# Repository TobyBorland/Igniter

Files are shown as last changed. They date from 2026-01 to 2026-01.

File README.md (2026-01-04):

# Igniter
Analogue igniter circuit for transistorised ignition with mechanical advance

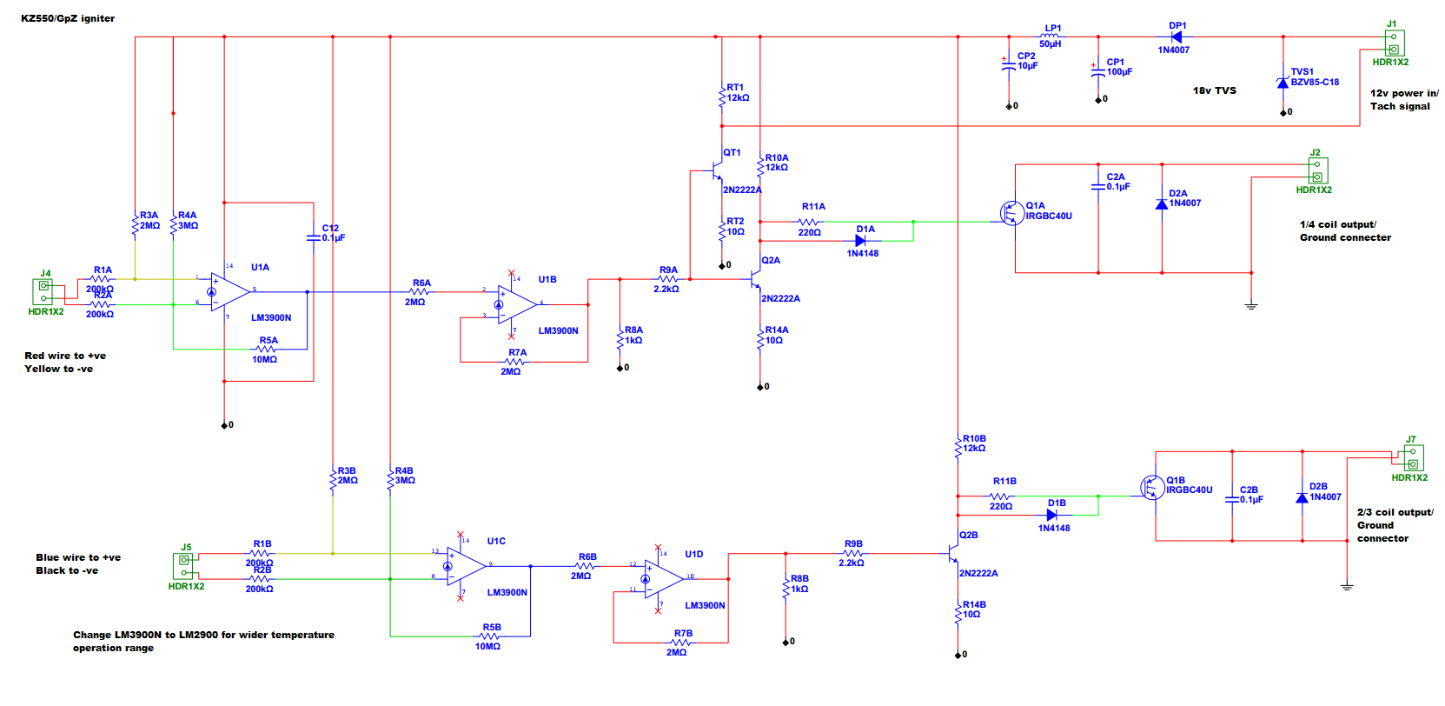
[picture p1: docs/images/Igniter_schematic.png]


### Kettering ignition
This project replaces the igniter used in earlier transistorised Kettering vehicle ignition. 
Old **points** ignition systems use a form of transformer (commonly referred to as an ignition coil) to create a spark for a petrol engine. 
During operation, the low-tension (LT) coil in this transformer is energised with 12 volts, creating a magnetic field. 
When the spark is required, the power is cut to the low-voltage coil, and the magnetic field in the coil transformer collapses, sending energy through the coupled high-tension coil. 
The high-tension coil output has lower resistance to current flow than the low-tension coil as it has more windings and generates higher voltage at lower amps, allowing the circuit to flow through a sparkplug air gap rather than the low-tension coil circuit. This Kettering system is simple and the current through the LT coil can be switched with a mechanical switch, "points" following a cam driven by the engine. A capacitor (**condensor**) is added to the 12v side of the circuit to give the points sufficient time to create a large air gap and force energy discharge through the HT side of the coil transformer. 
The timing of this spark ignition changes relative to the rotational speed of the engine; ignition occurs just after the piston starts a downward cycle in order to reduce mechanical shock. The optimal time to ignite the fuel mixture after the pistons change in direction varies with engine speed, Kettering mechanical systems use a simple mechanical spark advance mechanism which alters the switching points position relative to the cam operating the switch. The cam profile is designed to provide current to the coil for enough time to create a magnetic field powerful enough for an adequate spark. This field generation time is known as **dwell**.
However, switching several amps of current through mechanical contacts at several thousand cycles per minute causes wear and spark erosion. These switch point contacts have to be regularly adjusted, cleaned and replaced. The springs that close these points contacts are of variable quality and strength, and this process of regular servicing is a drawback to old vehicles.
### Transistor-assisted ignition
Manufacturers then adopted power transistors to perform the task of the points switching, this is the "igniter" used in 1980s transistorised Kettering ignition design, before the adoption of capacitor discharge ignition, **CDI**, which uses a switched capacitor discharge through a step-up transformer to create the spark. These early systems still used the same mechanical spark timing advancer. 

Early transistorised ignition placed a magnet on the crankshaft to generate an electrical signal in a nearby "pick-up" coil, a variable reluctance sensor similar to a magnetic tape head. This signal then switched the transistor controlling 12 volt power to the ignition coil. Later designs adopted Hall-effect sensors to detect crankshaft position from a passing magnet and a microprocessor to calculate the spark advance timing. 

I had tried several aftermarket ignition systems and found reliability to be an issue. Cheaper aftermarket systems would place the power transistors inside the points cover, where engine heat and high current would cause them to prematurely fail. Hall-effect pickups are also more sensitive to heat than simple pick-up coils, call-out mechanics would describe these as the most common failure that would strand a vehicle. While this transistorised Kettering design is simple and reliable, 1980s electronics eventually die.

As the design of high power transistors has improved since the 1980's, it seemed rational to create a reliable igniter using the original pick-ups to switch standard ignition coils. Several designs already exist which use a low-power transistor to switch the power-transistor, people have used ignition modules from cars or designed signal-conditioning circuitry to operate with the signal from pick-up coils with varying success. The disadvantage with the signal from an inductive pick-up coil is that it creates a low voltage pulse at low speed and a high voltage pulse at high speed. Any signal detection that relies on the voltage passing a set threshold would vary with engine speed.

A second problem with this design is that the dwell, or duration the coil is energised, cannot be established from a single signal without adding digital processing or some equivalent bucket-brigade analogue circuit. I found that manufacturers used a **Constant Energy** design to address this requirement. The magnetic pickup signal was designed so that the duration of the pulse would give two signals, beginning where the signal crossed a set threshold and ending where the signal dropped below a second threshold. 
The duration of this value corresponded roughly to the dwell requirements at a specific RPM, i.e. a constant energy is supplied to the coils at all engine speeds.
Measuring this pick-up coil voltage revealed a problem; the variation between peak voltage at high RPM and low RPM is considerable, making the design of accurate circuitry operating across this range complex. Instead of using clipping diodes on the voltage signal, I found that the current signal provided a consistent signal shape across RPM while retaining the duration required for dwell. The design here uses a current op-amp (or Norton amp) to generate a square-wave power transistor trigger signal at set current values. 

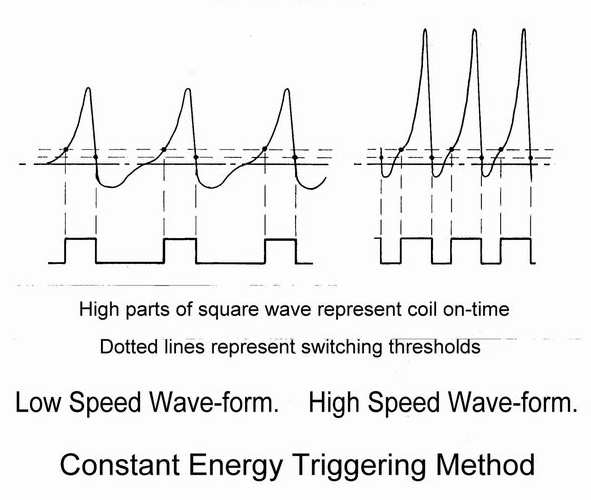
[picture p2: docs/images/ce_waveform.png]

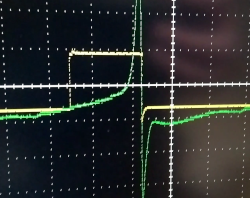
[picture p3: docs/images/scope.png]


### Signal conditioning
The ancient LM3900 is a quadruple current differencing op-amp, in the [technical notes](https://www.ti.com/lit/an/snoa653/snoa653.pdf?ts=1767440537261) a "squaring amplifier" is described creating a clean square-wave signal based on the input from a variable reluctance transducer, or inductive pick-up. With slight variations of resistance values to adapt to the intended signal start and stop thresholds, this circuit is an elegant solution to pick-up signal conditioning with minimum components. The LM2900 is a similar chip that operates across wider temperature range.

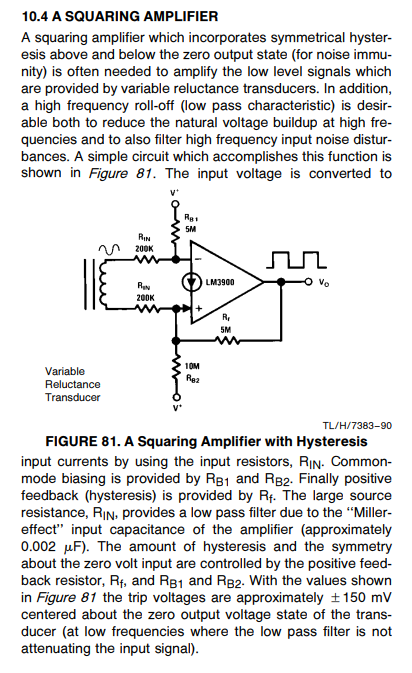
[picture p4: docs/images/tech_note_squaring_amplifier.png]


### IGBT switching
The main switching transistors used in this design are N-channel Insulated Gate Bipolar Transistors, IRGBC40U. The advantage of these modern designs they have the high current and voltage switching capacity associated with power MOSFETs but do not require the additional driver circuitry to switch MOSFET gates. These IGBT gates are driven by common 2N2222 transistors with a diode and resistor network to allow rapid gate charge drain. Each IGBT has an additional 1N4007 diode to reduce the counter EMF voltage at the transistor, along with a high-voltage capacitor to dampen the voltage spike during switching. Note that the heatsink tab of the TO220 case should not be electrically connected to ground, and insulation is required for an earthed heatsink.

As there are no digital components in this circuit, nor particularly delicate components, the power filtering uses an 18 volt transient voltage suppression diode and a low-pass filter based around inductors from an ATX PC power supply. There is a diode to protect against reverse polarity. Finally there is a separate 12v square wave signal driven by an independent transistor for the purpose of a digital tachometer signal. 

The board design uses chunky screw connectors for the pick-ups coils and ignition coil connections. These are best changed for soldered wires terminated in the bullet and block connecters for the motorcycle model. This prototype design used a large diecast metal box for heat dissipation and component access. In retrospect this turned out to be a reliable design that does not transfer much heat and can use a simple plate heatsink with component epoxy potting. So far around 20,000 miles without issue in ambient temperature from -5C to 42C.
If using this design with a Kawasaki KZ650/Z650, GT550 etc, the mechanical advancer must be changed for the advancer used with transistorised ignition models. 

The Gerber RS274X files are accepted by most PCB manufacturers, this is a double-sided board using through-hole plating. Solder the resistors first, and clean flux off the board prior to use, particularly around high value resistors. I used a conformal acrylic coating over the finished board to improve resistance to the elements. This ignition is being used with Kawasaki LTD Spectre magnetic pickups, 5 ohm ignition coils and 7mm silicone/graphite HT cables. Note that it is safe to leave this ignition on without running the engine as it does not switch power to the coils when stationary.

### BOM

| Value | Silkscreen Outline | Number | Reference Designation | 
| --- | --- |  --- |  --- |
|0.1uF | CAPR1500-1700X650X1150 | 2 | C2A,C2B |
|0.1uF | KERKO6X5R5 | 1| C12| 
|1N4007 | DO-41| 3| D2A,D2B,DP1|  
|1N4148| DO-35| 2| D1A,D1B| 
|1kOhm| R0204R7_5| 2| R8A,R8B| 
|2.2kOhm | R0204R7_5| 2| R9A,R9B| 
|2MOhm| R0204R7_5| 1| R3A| 
|2MOhm| R0204R7_5| 3| R3B,R7A,R7B|  
|2MOhm| R0204R10| 2| R6A,R6B |
|2N2222A| TO-92(Bent)|  3| Q2A,Q2B,QT1  |
|3MOhm| R0204R7_5| 2| R4A,R4B |
|10MOhm| R0204R7_5| 2| R5A,R5B |
|10uF| ELKO5R2_5| 1| CP2 |
|10Ohm| R0204R7_5| 3| R14A,R14B,RT2|
|12kOhm| R0204R7_5| 3| R10A,R10B,RT1|
|50uH| DRO_TDK14X8|  1| LP1 |
|100uF| ELKO8R3_5| 1| CP1 |
|200kOhm| R0204R7_5| 4| R1A,R1B,R2A,R2B|
|220Ohm| R0204R7_5| 2| R11A,R11B |
|BZV85-C18| DIO_P6KE_V| 1| TVS1 |
|HDR1X2| SMK2R5MIL_A|  4| J1,J2,J4,J7  |
|HDR1X2| SMK2R5MM_A| 1| J5 |
|IRGBC40U| TO220V| 2| Q1A,Q1B |
|LM3900N| DIP14300| 1| U1  |

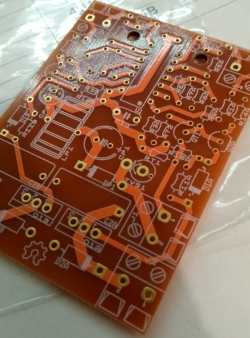
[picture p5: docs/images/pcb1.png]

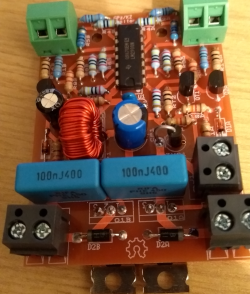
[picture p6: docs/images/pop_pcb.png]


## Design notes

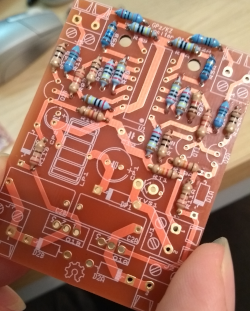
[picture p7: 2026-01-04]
docs/images/pcb2.png
